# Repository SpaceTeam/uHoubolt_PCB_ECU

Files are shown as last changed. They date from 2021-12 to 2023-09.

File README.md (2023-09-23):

# µHoubolt Engine Control Unit (ECU) Hardware

## Features
- 3 RC Servo outputs with position feedback and current measurement
- 2 High-current low side FET outputs with current measurement
- 3 Pyro outputs with high side switch (supplied separately from main supply), continuity check, current measurement and current limiting
- 6 Pressure sensor inputs, individually configurable for 0-150mV differential, 0-5V single ended and 4-20mA
- 3 Temperature sensor inputs for resistive types
- Status LEDs on all outputs, voltage rails and two user programmable
- 2 CAN-FD buses, multiple connectors per bus for simple daisy-chaining
- Debug interface with SWD and UART
- 70x40mm 4-layer PCB, additional power and CAN connectors on back side

## Known Issues
- Wrong Footprint for STM
- Igniter continuity check not working without Pyro voltage
- Missing low pass filter for servo current measurement
- Switching on the 12V supply (or power cycling it) when the pyro supply is already active can initiate igniters (poblematic in combination with issue in PMU, see PMU Known Issues and EuRoC flight report). Pull down resistors on igniter enable lines are missing.
- Using current sense amps for the pressure sensor inputs is bad, their low input impedance significantly reduces the measured values. Wasn't a problem (and wasn't even noticed?) as the measurements are still linear (tested by GATE) and the sensors were calibrated against a Baluff sensor, but should be avoided in future revisions by using instrumentation amplifiers (e.g. INA350).

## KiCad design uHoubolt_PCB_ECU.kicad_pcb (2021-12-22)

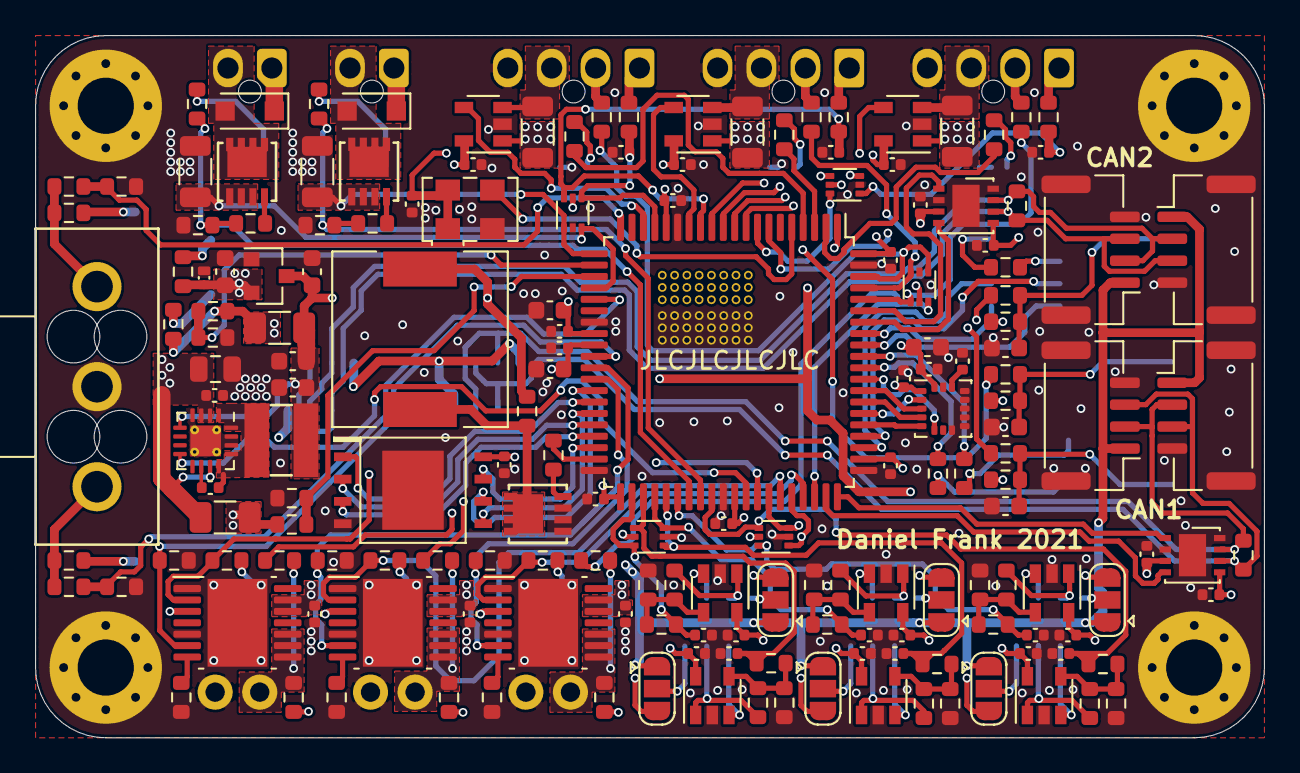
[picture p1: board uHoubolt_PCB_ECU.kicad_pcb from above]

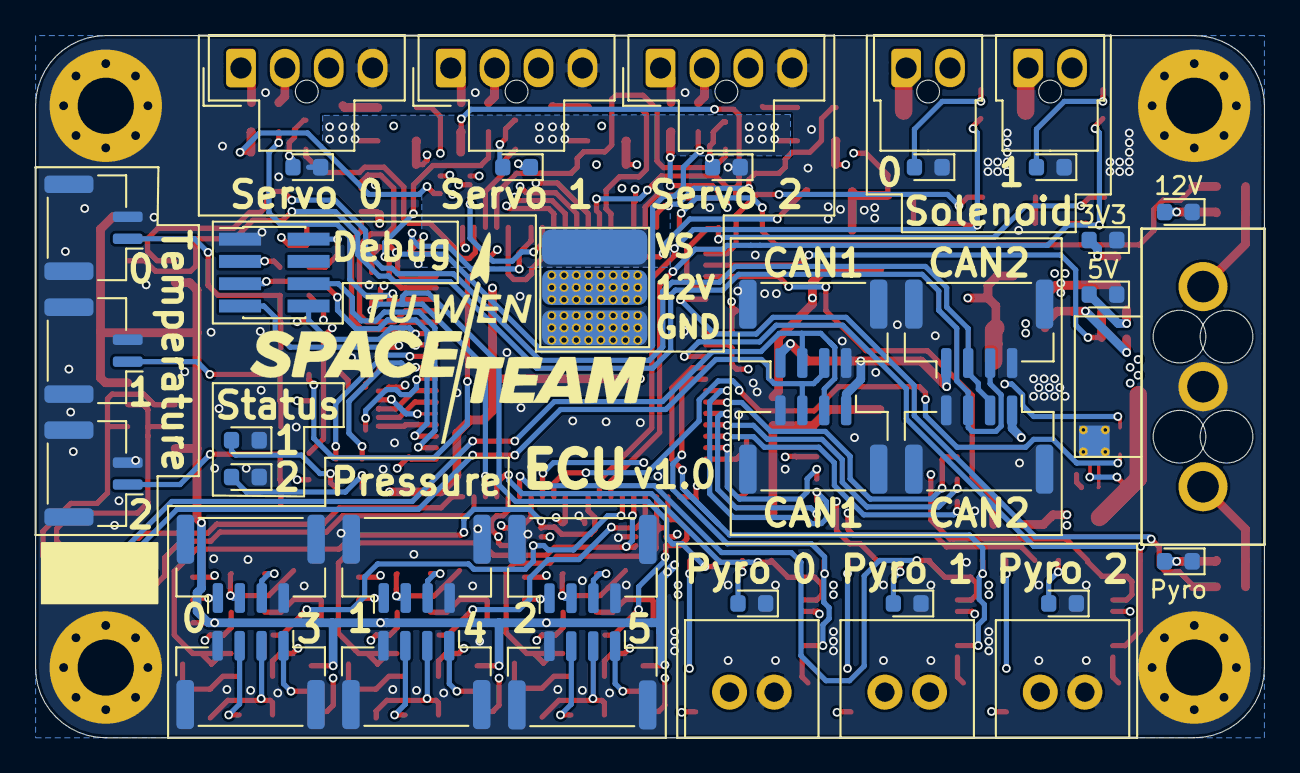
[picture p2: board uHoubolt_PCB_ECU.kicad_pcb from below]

Board: 4 copper layers, 70.0 x 40.0 mm, 216 parts (38 on the bottom side), 140 nets.

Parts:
C1, C2, C12, C17, C21, C22, C23, C24, C25, C26, C27, C30, C31, C32, C33, C34, C35, C37, C38, C39, C40, C41, C43, C44, C45, C46, C47, C48, C49, C50, C51, C52, C53, C56, C57, C58, C59, C60, C61: 100n; C_0402_1005Metric
C10: 10µ; C_0805_2012Metric
C16, C20, C28, C29, C36: 2µ2; C_0603_1608Metric
C18, C19, C42, C54, C55: 22µ; C_0603_1608Metric
D1: VIN; LED_0603_1608Metric
D2: PYRO; LED_0603_1608Metric
D3: 5V; LED_0603_1608Metric
D4: LED 1; LED_0603_1608Metric
D5: LED 2; LED_0603_1608Metric
D6, D9: OUT 1; LED_0603_1608Metric
D7, D10: Shottky; D_SOD-123F
D8, D11, D12: PYRO 1; LED_0603_1608Metric
D13: TVS 3V3; SOD882D
D14, D15, D16: Servo; LED_0603_1608Metric
D17: 3V3; LED_0603_1608Metric
F1, F2: 350mA; Fuse_1206_3216Metric
G1: SpaceTeam_LOGO; ST_Logo_new
H1, H2, H3, H4: MH; MountingHole_3.2mm_M3_Pad_Via
J1: Power In; Molex_MegaFit_1x03_Vertical_Doublesided
J2: Debug; PinHeader_2x04_P1.27mm_Vertical_SMD
J3, J5, J35, J37: CAN1; JST_GH_BM04B-GHS-TBT_1x04-1MP_P1.25mm_Vertical
J4, J6, J36, J38: CAN2; JST_GH_BM04B-GHS-TBT_1x04-1MP_P1.25mm_Vertical
J7, J12, J13, J14, J15, J23: Pressure; JST_GH_BM04B-GHS-TBT_1x04-1MP_P1.25mm_Vertical
J8, J16, J17: TEMP; JST_GH_BM02B-GHS-TBT_1x02-1MP_P1.25mm_Vertical
J9, J18, J19: Servo; Molex_Nano-Fit_105309-xx04_1x04_P2.50mm_Vertical
J10, J20: Solenoid; Molex_Nano-Fit_105309-xx02_1x02_P2.50mm_Vertical
J11, J21, J22: Pyro; Molex_SL_1x2_Vertical
JP1, JP3, JP4, JP5, JP6, JP7: V_SEL; SolderJumper-3_P1.3mm_Open_RoundedPad1.0x1.5mm
JP2: Servo Voltage Select; Jumper3_6x2mm_Vias23
L2: 4µ7; SRN4018TA-4R7M
LS1: Speaker; Piezo_Buzzer
Q1, Q2, Q3: SISA88DN or similar; PowerPAK_1212-8
R1, R21, R37, R40, R43, R46: 5k6/0; R_0603_1608Metric
R2, R22, R38, R41, R44, R47: 10k/160; R_0603_1608Metric
R3, R6, R24, R27, R35, R49, R50, R53, R56, R64, R69, R75, R76, R78: 1k; R_0603_1608Metric
R4, R8, R12, R33, R34, R36, R62, R63, R65, R67, R68, R70: 56k; R_0603_1608Metric
R5, R7, R9, R13, R14, R15, R16, R23, R25, R29, R39, R42, R45, R48, R51, R54, R58, R71, R72, R73: 10k; R_0603_1608Metric
R10, R11, R17, R18, R19, R20, R28, R30, R32, R57, R59, R61, R66, R74, R77: 120; R_0603_1608Metric
R26, R31, R52, R55, R60: 10m 1W; R_1206_3216Metric
U1, U9, U10, U12, U13, U14, U15, U16, U17: INA180B1; SOT-23-5
U2: TS30041-M050QFNR; QFN-16-1EP_3x3mm_P0.5mm_EP1.75x1.75mm_ThermalVias
U3: MCP1700-3302E; SOT-23
U4, U5: MCP2562FDx-x_MF; DFN-8-1EP_3x3mm_P0.65mm_EP1.55x2.4mm
U6: STM32G491MET6-LQFP80; LQFP-80_14x14mm_P0.65mm
U7: ICM-20602; LGA-16_3x3mm_P0.5mm_LayoutBorder3x5y
U8: W25Q256JV; WSON-8-8x6mm
U11, U18, U19: TPS1HC100; HTSSOP-14-1EP_4.4x5mm_P0.65mm_EP3.4x5mm_Mask3x3.1mm
U20, U21, U22, U23, U24: D1213A-04V; SOT-563
X1: TXC-7C; Oscillator_SMD_TXC_7C-4Pin_5.0x3.2mm

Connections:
+3V3: C1.1, C20.2, C21.1, C22.1, C23.1, C24.1, C25.2, C28.2, C29.2, C30.2, C31.2, C32.2, C33.2, C34.2, C35.2, C36.1, C37.1, C38.1, C39.2, C44.1, C46.1, C48.1, C50.1, C52.1, C57.1, C59.1, D13.1, J2.2, R16.2, R24.1, R34.2, R49.1, R50.1, R63.2, R68.2, R76.1, U1.5, U3.2, U4.5, U5.5, U6.1, U6.16, U6.28, U6.29, U6.41, U6.51, U6.62, U6.80, U7.1, U7.16, U8.8, U9.5, U10.5, U11.3, U12.5, U13.5, U14.5, U15.5, U16.5, U17.5, U18.3, U19.3, U20.5, U21.5, U22.5, U23.5, U24.5, X1.1, X1.4
+5V: F1.1, J3.1, J4.1, J5.1, J6.1, J35.1, J36.1, J37.1, J38.1, JP1.1, JP3.1, JP4.1, JP5.1, JP6.1, JP7.1, R14.1, R75.1
+12V: C10.1, C12.1, D7.1, D10.1, F2.2, J1.1, J10.1, J20.1, JP2.2, LS1.1, R3.1, R4.1, R78.1, U2.2, U2.3, U2.11
+12VA: F2.1, JP1.3, JP3.3, JP4.3, JP5.3, JP6.3, JP7.3, R12.1
/5V_PGOOD: U2.8, U6.52
/5V_SENSE: R14.2, R15.1, U6.22
/5V_unfused: C16.2, C18.1, C19.1, C26.1, C27.1, F1.2, L2.2, U2.5, U3.3, U4.3, U5.3
/12VA_SENSE: R12.2, R13.1, U6.23
/12V_SENSE: R4.2, R5.1, U6.20
/CAN1_H: J3.2, J5.2, J35.2, J37.2, R17.1, U4.7
/CAN1_L: J3.3, J5.3, J35.3, J37.3, R17.2, U4.6
/CAN1_RX: U4.4, U6.59
/CAN1_TX: U4.1, U6.60
/CAN2_H: J4.2, J6.2, J36.2, J38.2, R18.1, U5.7
/CAN2_L: J4.3, J6.3, J36.3, J38.3, R18.2, U5.6
/CAN2_RX: U5.4, U6.74
/CAN2_TX: U5.1, U6.75
/CLK: U6.5, X1.3
/IMU_INT: U6.69, U7.6
/LED_1: R19.2, U6.71
/LED_2: R20.2, U6.70
/NRST: J2.3, R16.1, U6.7
/PRESS_0: C41.1, R23.2, U6.46, U23.6
/PRESS_1: C53.1, R48.2, U6.44, U24.3
/PRESS_2: C2.1, R7.2, U6.42, U24.6
/PRESS_3: C51.1, R45.2, U6.49, U23.4
/PRESS_4: C49.1, R42.2, U6.45, U24.1
/PRESS_5: C47.1, R39.2, U6.43, U24.4
/PYRO_0_CONT: R36.1, U6.58, U22.6
/PYRO_0_CTRL: R32.1, U6.57, U11.2
/PYRO_0_CURR: R35.2, U6.32, U11.6
/PYRO_1_CONT: R65.1, U6.56, U23.1
/PYRO_1_CTRL: R61.1, U6.55, U18.2
/PYRO_1_CURR: R64.2, U6.31, U18.6
/PYRO_2_CONT: R70.1, U6.54, U23.3
/PYRO_2_CTRL: R66.1, U6.53, U19.2
/PYRO_2_CURR: R69.2, U6.30, U19.6
/PYRO_SENSE: R8.2, R9.1, U6.25
/QSPI1_BK1_IO0: U6.35, U8.5
/QSPI1_BK1_IO1: U6.36, U8.2
/QSPI1_BK1_IO2: U6.37, U8.3
/QSPI1_BK1_IO3: U6.38, U8.7
/QSPI1_BK1_NCS: U6.34, U8.1
/QSPI1_CLK: U6.33, U8.6
/SERVO_0_CURR: U6.12, U10.4
/SERVO_0_FDBK: C43.1, R25.1, U6.11, U21.1
/SERVO_0_LED: R10.1, U6.2
/SERVO_0_PWM: R27.1, U6.76, U22.4
/SERVO_1_CURR: U6.14, U17.4
/SERVO_1_FDBK: C58.1, R54.1, U6.13, U20.6
/SERVO_1_LED: R74.1, U6.3
/SERVO_1_PWM: R56.1, U6.77, U22.3
/SERVO_2_CURR: U6.18, U16.4
/SERVO_2_FDBK: C56.1, R51.1, U6.17, U20.4
/SERVO_2_LED: R11.1, U6.4
/SERVO_2_PWM: R53.1, U6.78, U22.1
/SOLENOID_0_CTRL: R57.1, R58.2, R59.1, U6.48
/SOLENOID_0_CURR: Q2.3, R60.1, U6.21, U20.1
/SOLENOID_1_CTRL: R28.1, R29.2, R30.1, U6.47
/SOLENOID_1_CURR: Q1.3, R31.1, U6.24, U20.3
/SPI_IMU_CS: U6.65, U7.5
/SPI_MISO: U6.67, U7.4
/SPI_MOSI: U6.68, U7.3
/SPI_SCK: U6.66, U7.2
/SWCLK: J2.5, U6.64
/SWDIO: J2.6, U6.63
/Speaker: R77.1, U6.39
/TEMP_0: R73.1, U6.8, U21.6
/TEMP_1: R71.1, U6.9, U21.4
/TEMP_2: R72.1, U6.10, U21.3
/UART_RX: J2.8, U6.73
/UART_TX: J2.7, U6.72
GND: C1.2, C2.2, C10.2, C12.2, C16.1, C18.2, C19.2, C20.1, C21.2, C22.2, C23.2, C24.2, C25.1, C26.2, C27.2, C28.1, C29.1, C30.1, C31.1, C32.1, C33.1, C34.1, C35.1, C36.2, C37.2, C38.2, C39.1, C40.1, C41.2, C42.1, C43.2, C44.2, C45.2, C46.2, C47.2, C48.2, C49.2, C50.2, C51.2, C52.2, C53.2, C54.1, C55.1, C56.2, C57.2, C58.2, C59.2, C60.2, C61.2, D1.1, D2.1, D3.1, D4.1, D5.1, D6.1, D8.1, D9.1, D11.1, D12.1, D13.2, D14.1, D15.1, D16.1, D17.1, H1.1, H2.1, H3.1, H4.1, J1.2, J2.1, J3.4, J3.MP, J4.4, J4.MP, J5.4, J5.MP, J6.4, J6.MP, J7.4, J7.MP, J8.2, J8.MP, J9.4, J11.1, J12.4, J12.MP, J13.4, J13.MP, J14.4, J14.MP, J15.4, J15.MP, J16.2, J16.MP, J17.2, J17.MP, J18.4, J19.4, J21.1, J22.1, J23.4, J23.MP, J35.4, J35.MP, J36.4, J36.MP, J37.4, J37.MP, J38.4, J38.MP, JP2.3, Q3.3, R2.2, R5.2, R9.2, R13.2, R15.2, R22.2, R29.1, R31.2, R33.1, R35.1, R38.2, R41.2, R44.2, R47.2, R58.1, R60.2, R62.1, R64.1, R67.1, R69.1, U1.2, U2.4, U2.14, U2.15, U2.17, U3.1, U4.2, U4.8, U4.9, U5.2, U5.8, U5.9, U6.15, U6.27, U6.40, U6.50, U6.61, U6.79, U7.8, U7.9, U7.10, U7.11, U7.12, U7.13, U7.15, U8.4, U8.9, U9.2, U10.2, U11.1, U11.5, U11.15, U12.2, U13.2, U14.2, U15.2, U16.2, U17.2, U18.1, U18.5, U18.15, U19.1, U19.5, U19.15, U20.2, U21.2, U22.2, U23.2, U24.2, X1.2
unnamed: C17.1, U2.10
unnamed: C17.2, L2.1, U2.1, U2.12, U2.13, U2.16
unnamed: C40.2, U7.14
unnamed: C42.2, J8.1, R24.2, R71.2
unnamed: C54.2, J16.1, R49.2, R72.2
unnamed: C55.2, J17.1, R50.2, R73.2
unnamed: D1.2, R3.2
unnamed: D2.2, R6.2
unnamed: D3.2, R75.2
unnamed: D4.2, R19.1
unnamed: D5.2, R20.1
unnamed: D6.2, R28.2
unnamed: D7.2, J10.2, Q1.2
unnamed: D8.2, R32.2
unnamed: D9.2, R57.2
unnamed: D10.2, J20.2, Q2.2
unnamed: D11.2, R61.2
unnamed: D12.2, R66.2
unnamed: D14.2, R10.2
unnamed: D15.2, R11.2
unnamed: D16.2, R74.2
unnamed: D17.2, R76.2
unnamed: J7.1, JP1.2
unnamed: J7.2, R21.1, U9.1
unnamed: J7.3, U9.3
unnamed: J9.1, R25.2
unnamed: J9.2, R27.2
unnamed: J9.3, R26.1, U10.3
unnamed: J11.2, R34.1, R36.2, U11.8, U11.9, U11.10
unnamed: J12.1, JP4.2
unnamed: J12.2, R37.1, U12.1
unnamed: J12.3, U12.3
unnamed: J13.1, JP5.2
unnamed: J13.2, R40.1, U13.1
unnamed: J13.3, U13.3
unnamed: J14.1, JP6.2
unnamed: J14.2, R43.1, U14.1
unnamed: J14.3, U14.3
unnamed: J15.1, JP7.2
unnamed: J15.2, R46.1, U15.1
unnamed: J15.3, U15.3
unnamed: J18.1, R51.2
unnamed: J18.2, R53.2
unnamed: J18.3, R52.1, U16.3
unnamed: J19.1, R54.2
unnamed: J19.2, R56.2
unnamed: J19.3, R55.1, U17.3
unnamed: J21.2, R63.1, R65.2, U18.8, U18.9, U18.10
unnamed: J22.2, R68.1, R70.2, U19.8, U19.9, U19.10
unnamed: J23.1, JP3.2
unnamed: J23.2, R1.1, U1.1
unnamed: J23.3, U1.3
unnamed: LS1.2, Q3.2, R78.2
unnamed: Q1.1, R30.2
unnamed: Q2.1, R59.2
unnamed: Q3.1, R77.2
unnamed: R1.2, R2.1, R7.1, U1.4
unnamed: R21.2, R22.1, R23.1, U9.4
unnamed: R33.2, U11.7
unnamed: R37.2, R38.1, R39.1, U12.4
unnamed: R40.2, R41.1, R42.1, U13.4
unnamed: R43.2, R44.1, R45.1, U14.4
unnamed: R46.2, R47.1, R48.1, U15.4
unnamed: R62.2, U18.7
unnamed: R67.2, U19.7
PYRO: C45.1, C60.1, C61.1, J1.3, R6.1, R8.1, U11.12, U11.13, U18.12, U18.13, U19.12, U19.13
VS: JP2.1, R26.2, R52.2, R55.2, U10.1, U16.1, U17.1

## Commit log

2020-11-16 create kicad project with library paths
    [uHoubolt_PCB_FCU.kicad_pcb, uHoubolt_PCB_FCU.sch]
2020-11-17 fix library path
    [uHoubolt_PCB_FCU.sch]
2020-12-03 add mcu schematic
    [uHoubolt_PCB_FCU.sch]
2020-12-17 add power symbols
    [uHoubolt_PCB_FCU.sch]
2021-02-25 add 10A solenoid circuit
    [uHoubolt_PCB_FCU.sch]
2021-02-25 add 5V Zünder circuit
    [uHoubolt_PCB_FCU.sch]
2021-02-25 add continuity sense to 5V Zünder circuit
    [uHoubolt_PCB_FCU.sch]
2021-04-12 add 2x variable input pressure sensor circuit
    [uHoubolt_PCB_FCU.sch]
2021-05-08 Added modules from Trello list. Todo: Review, assign pins to labels, component naming.
    [uHoubolt_PCB_FCU.sch]
2021-05-30 Changed IMU and assigned sigs to uC pins.
    [uHoubolt_PCB_FCU.sch]
2021-08-11 Implemented changes after design review
    [uHoubolt_PCB_FCU.sch]
2021-11-05 cleanup of file structure
    [MCU_Periphery.sch, REG5V.sch, uHoubolt_PCB_ECU.kicad_pcb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]
2021-11-10 schematic mostly done
    [MCU_Periphery.sch, REG5V.sch, uHoubolt_PCB_ECU.kicad_pcb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]
2021-11-16 schematic even more done
    [uHoubolt_PCB_ECU.kicad_pcb, uHoubolt_PCB_ECU.sch]
2021-11-16 moved I/O to subsheets, started layout
    [HighCurrentOutput.sch, PressureSensorInput.sch, PyroOutput.sch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]
2021-11-17 preliminary placement done
    [HighCurrentOutput.sch, PressureSensorInput.sch, ServoOutput.sch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]
2021-11-17 small changes, added Step File
    [uHoubolt_PCB_ECU.kicad_pcb]
2021-11-18 changed form factor to better fit into uHb engine section
    [HighCurrentOutput.sch, PressureSensorInput.sch, PyroOutput.sch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]
2021-12-01 moved 7V4 buck to separate board
    [HighCurrentOutput.sch, PressureSensorInput.sch, PyroOutput.sch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]
2021-12-14 many small changes, before removing servo buck converter
    [HighCurrentOutput.sch, PressureSensorInput.sch, PyroOutput.sch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]
2021-12-14 placement almost done
    [HighCurrentOutput.sch, PressureSensorInput.sch, PyroOutput.sch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]
2021-12-14 fixed net names
    [HighCurrentOutput.sch, PressureSensorInput.sch, PyroOutput.sch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]
2021-12-15 schematic done, preliminary placement done
    [HighCurrentOutput.sch, PyroOutput.sch, ServoOutput.sch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]
2021-12-15 routing started
    [PressureSensorInput.sch, PyroOutput.sch, ServoOutput.sch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]
2021-12-19 routing done, drc clean (3 errors to be ignored)
    [PyroOutput.sch, ServoOutput.sch, TemperatureSensorInput.sch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]
2021-12-19 small improvements, updated doc
    [PressureSensorInput.sch, ServoOutput.sch, uHoubolt_PCB_ECU.kicad_pcb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]
2021-12-19 small changes, generated gerbers
    [PyroOutput.sch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]
2021-12-22 some more small changes
    [HighCurrentOutput.sch, PressureSensorInput.sch, PyroOutput.sch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]
2021-12-22 tiny changes, version to be ordered
    [uHoubolt_PCB_ECU-B_Cu.gbl, uHoubolt_PCB_ECU-B_Mask.gbs, uHoubolt_PCB_ECU-B_Paste.gbp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]
2022-01-01 updated to KiCad v6
    [HighCurrentOutput.kicad_sch, HighCurrentOutput.sch, PressureSensorInput.kicad_sch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]
2022-01-12 WIP v1.1, fixed JP2 footprint, replaced STM footprint, re-routing in progress
    [PressureSensorInput.kicad_sch, PyroOutput.kicad_sch, uHoubolt_PCB_ECU.kicad_sch]
